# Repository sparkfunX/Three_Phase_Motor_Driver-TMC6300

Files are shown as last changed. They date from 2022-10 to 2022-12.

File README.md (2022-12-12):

SparkFun 3-Phase BLDC Motor Driver - TMC6300
========================================

SparkFun 3-Phase BLDC Motor Driver - TMC6300 (https://www.sparkfun.com/products/21220)

[*SparkFun 3-Phase BLDC Motor Driver - TMC6300(ROB-21220)*](https://www.sparkfun.com/products/21220)

The TMC6300 from Trinamic is a powerful, yet easy to use three phase brushless DC (BLDC) motor driver. Separate high side and low side controls allow for incredible control up to 2A of current. The driver is temperature and short circuit protected with a diagnostic output pin to indicate system issues. With an operating voltage down to 2V, the TMC6300 is suitable for battery powered designs.

We've designed an innovative 2 sided, 4 layer breakout board to make hookup as easy as possible. The board is mounted with LEDs and labels facing up, IC down. This allows the thermal pad on the board to be access if cooling is required. 

Controlling 3-phase BLDC motors is not trivial. This board requires 6 PWM signals to fully control one motor. We've found the [*Arduino Simple Field Oriented Control*](https://docs.simplefoc.com/) library to be very good. The [open loop example](https://github.com/simplefoc/Arduino-FOC/blob/master/examples/motion_control/open_loop_motor_control/open_loop_velocity_example/open_loop_velocity_example.ino) combined with the [6 channel PWM method](https://docs.simplefoc.com/bldcdriver6pwm) and *every* PWM pin on the Arduino Uno gets this board working. Note the [pairs of PWM pins](https://docs.simplefoc.com/bldcdriver6pwm) that must be used. 

This board was designed to control our [3-phase Brushless Gimbal Stabilizer Motor](https://www.sparkfun.com/products/20441) but can be used with any 3-phase motor up to 2A.

SparkFun labored with love to create this code. Feel like supporting open source hardware? 
Buy a [breakout board](https://www.sparkfun.com/products/21220) from SparkFun!

Repository Contents
-------------------

* **/Documents** - Datasheet and User Manual
* **/Hardware** - Eagle design files (.brd, .sch)

License Information
-------------------

This product is _**open source**_! 

Please review the LICENSE.md file for license information. 

If you have any questions or concerns on licensing, please contact techsupport@sparkfun.com.

Please use, reuse, and modify these files as you see fit. Please maintain attribution to SparkFun Electronics and release any derivative under the same license.

Distributed as-is; no warranty is given.

- Your friends at SparkFun.

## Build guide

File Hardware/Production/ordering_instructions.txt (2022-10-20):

panel size, 108x118mm
PCB thickness, 1.6mm
number of layers, 4
soldermask color, Black
silkscreen color, White
oz copper, 1oz
finish, HASL lead free
stencils, none
pcs per panel, 30
min trace width, 0.1778mm / 0.0070in
min drill size, 0.3048mm / 0.0120in
filename to layer stackup 1/2/3/4: GTL, GL2, GL3, GBL

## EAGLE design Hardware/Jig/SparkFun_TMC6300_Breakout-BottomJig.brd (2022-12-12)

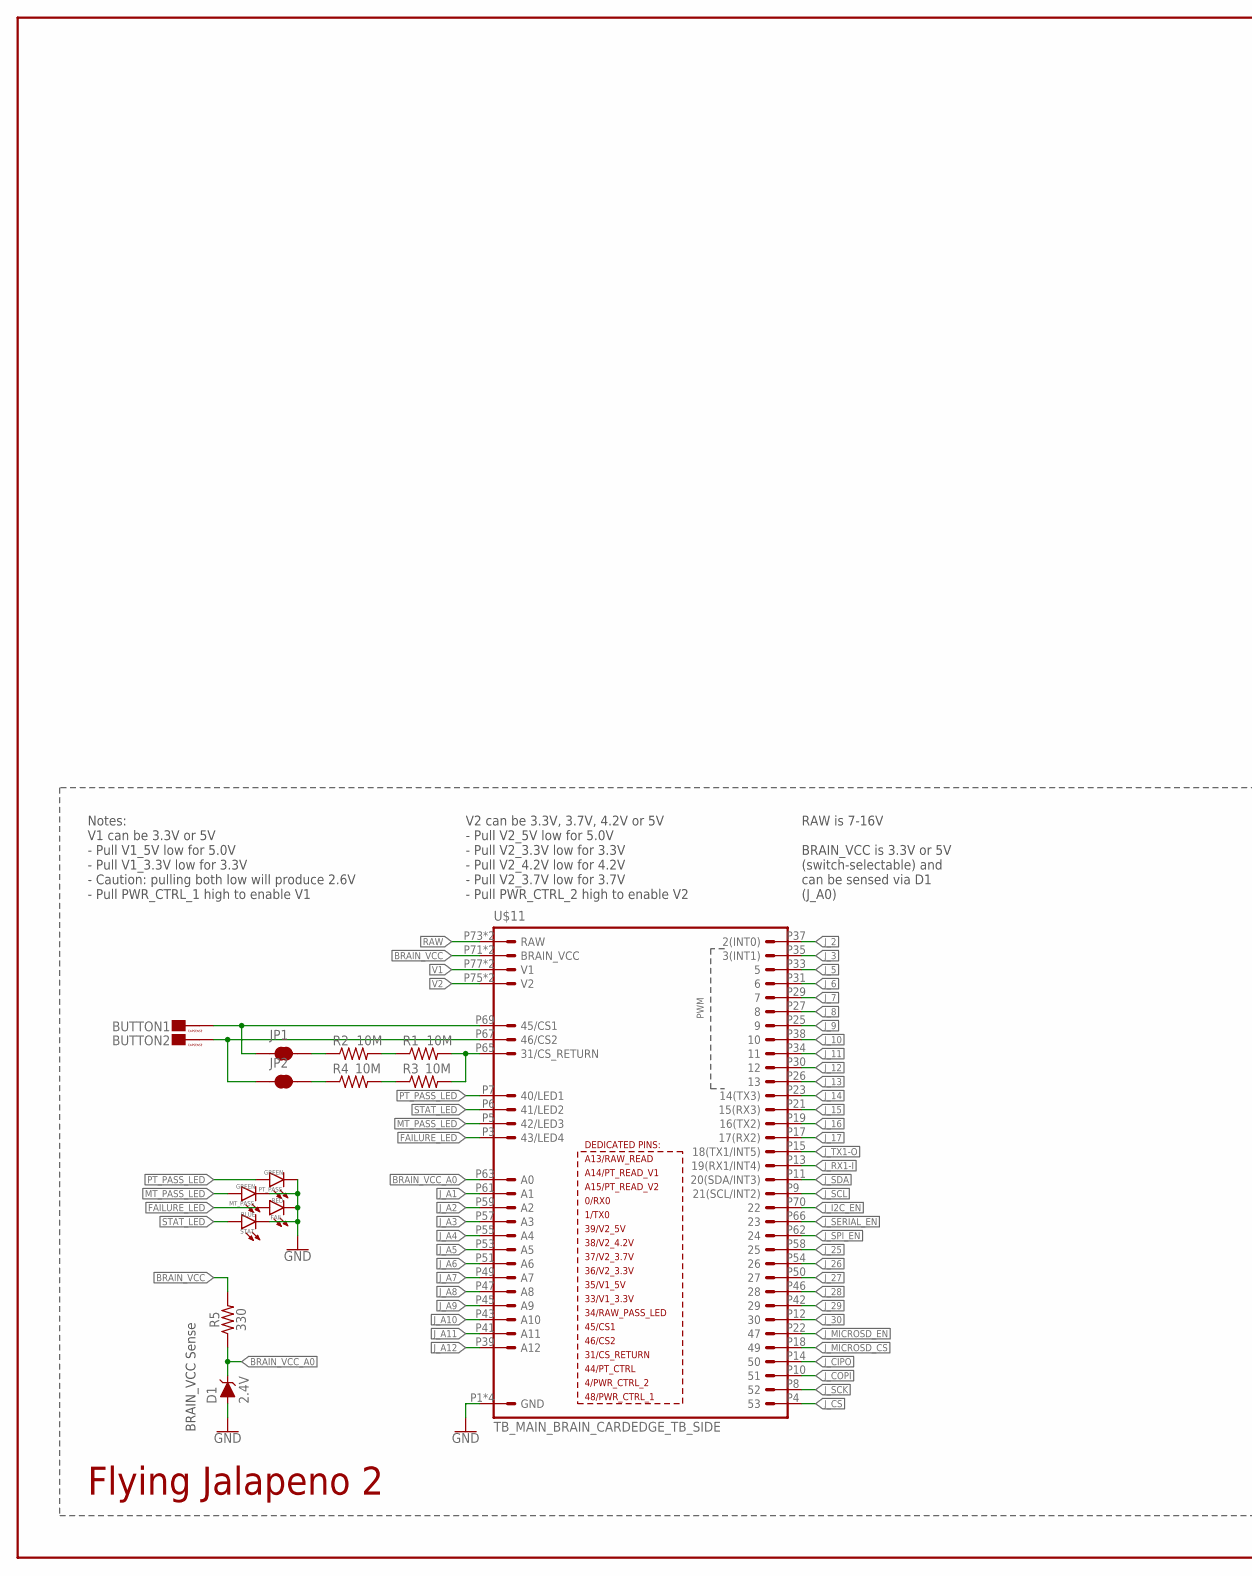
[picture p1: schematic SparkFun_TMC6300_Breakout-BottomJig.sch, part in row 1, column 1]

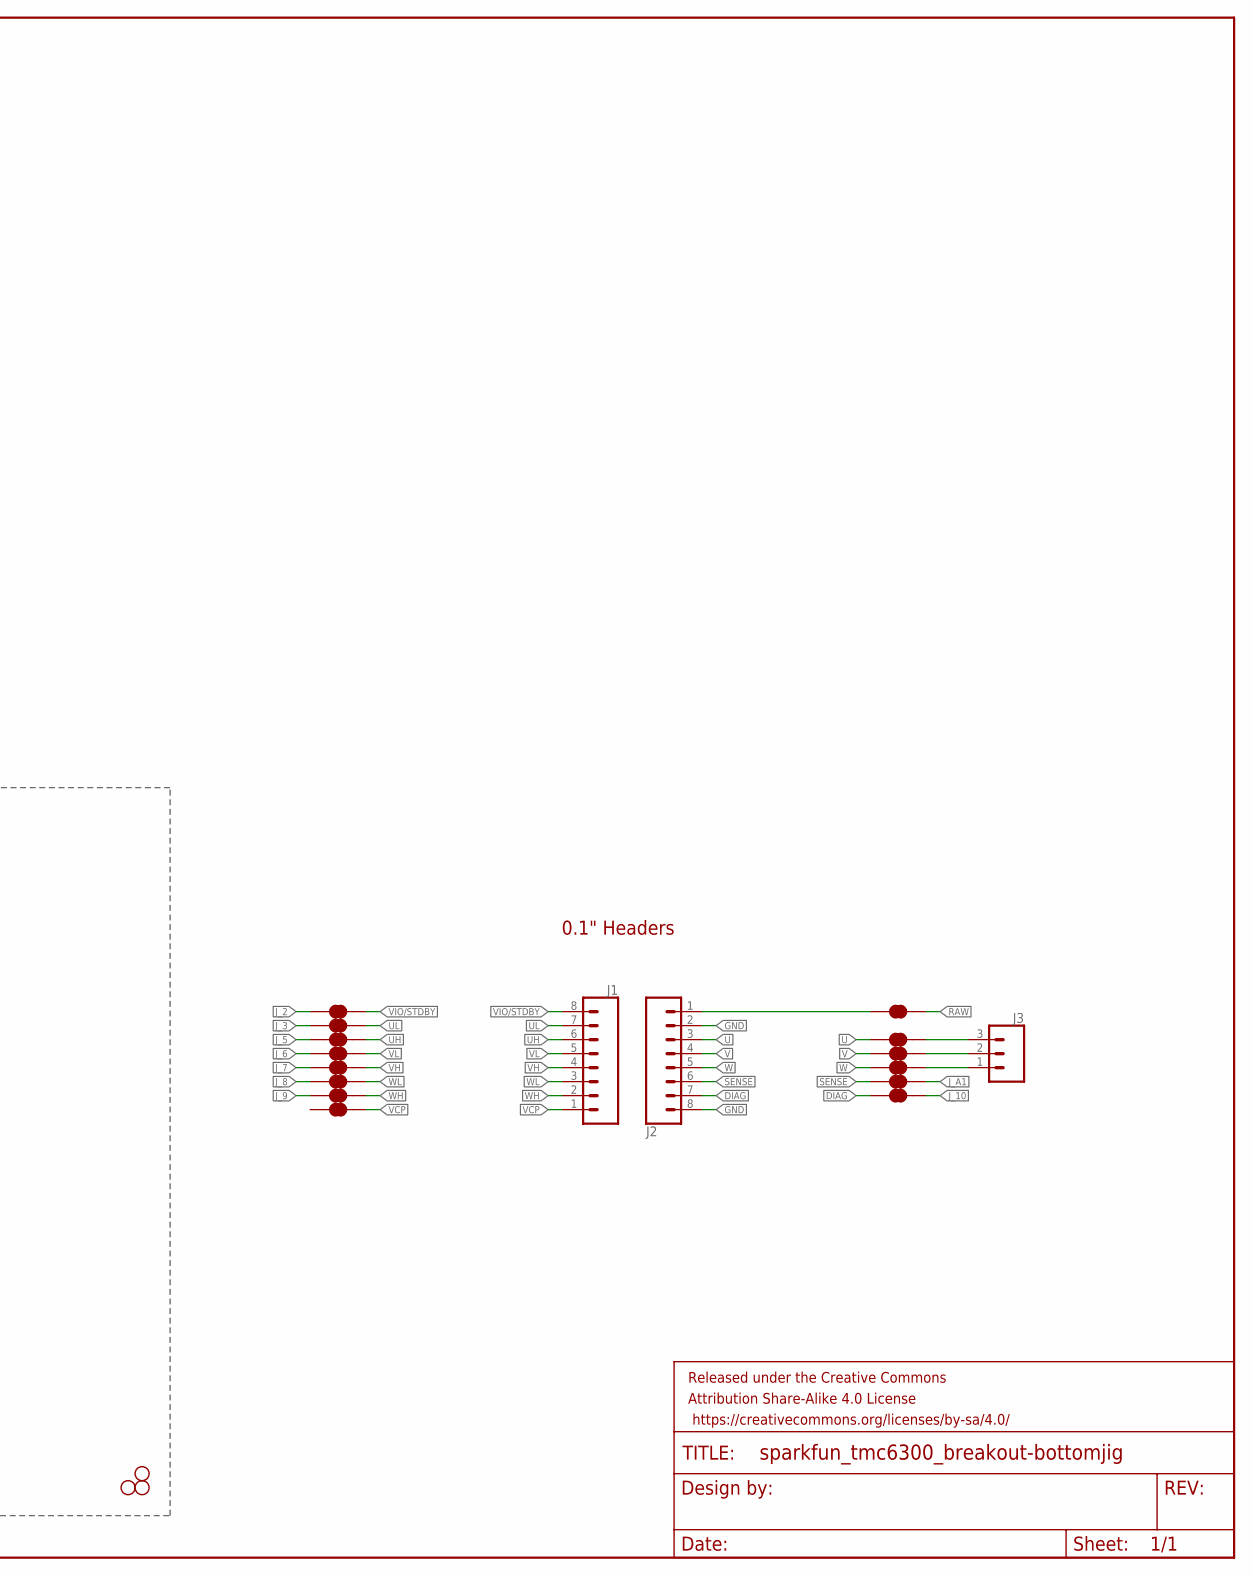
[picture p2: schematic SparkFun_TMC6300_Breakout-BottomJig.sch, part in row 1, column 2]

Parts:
BUTTON1, BUTTON2: CAPSENSE_BUTTON_PAD_ONLYV2_SMALL; CAPSENSE_BUTTON_PAD_ONLY_SM
D1: 2.4V; SOD-323
FAIL: RED; LED-1206
FRAME2: FRAME-LEDGER; CREATIVE_COMMONS
H1, H3, H4: STAND-OFF
J1, J2: CONN_08LOCK_NO_SILK; 1X08_LOCK_NO_SILK
J3: CONN_031X03_NO_SILK; 1X03_NO_SILK
JP1, JP2: JUMPER-SMT_2_NC_TRACE_SILK; SMT-JUMPER_2_NC_TRACE_SILK
J_SCL6, J_SCL7, J_SCL8: JUMPER-SMT_2_NC_TRACE_NO-SILK; SMT-JUMPER_2_NC_TRACE_NO-SILK
J_SDA1, J_SDA2, J_SDA3, J_SDA4, J_SDA5, J_SDA6, J_SDA7, J_SDA8, J_SDA9, J_SDA10, J_SDA11: JUMPER-SMT_2_NC_TRACE_NO-SILK; SMT-JUMPER_2_NC_TRACE_NO-SILK
MT_PASS: GREEN; LED-1206
PT_PASS: GREEN; LED-1206
R1, R2, R3, R4: 10M; 0603
R5: 330; 0603
STAT: BLUE; LED-1206
U$11: TB_MAIN_BRAIN_CARDEDGE_TB_SIDE; TB_CARDEDGE

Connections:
BRAIN_VCC: R5.2, U$11.P71 (BRAIN_VCC), U$11.P72 (BRAIN_VCC)
BRAIN_VCC_A0: D1.C, R5.1, U$11.P63 (A0)
DIAG: J2.7, J_SDA7.1
FAILURE_LED: FAIL.A, U$11.P3 (43/LED4)
GND: D1.A, FAIL.C, J2.2, J2.8, MT_PASS.C, PT_PASS.C, STAT.C, U$11.P1 (GND), U$11.P2 (GND), U$11.P79 (GND), U$11.P80 (GND)
J_2: J_SCL8.1, U$11.P37 (2(INT0))
J_3: J_SCL6.1, U$11.P35 (3(INT1))
J_5: J_SCL7.1, U$11.P33 (5)
J_6: J_SDA2.1, U$11.P31 (6)
J_7: J_SDA3.1, U$11.P29 (7)
J_8: J_SDA4.1, U$11.P27 (8)
J_9: J_SDA5.1, U$11.P25 (9)
J_10: J_SDA7.2, U$11.P38 (10)
J_11: U$11.P34 (11)
J_12: U$11.P30 (12)
J_13: U$11.P26 (13)
J_14: U$11.P23 (14(TX3))
J_15: U$11.P21 (15(RX3))
J_16: U$11.P19 (16(TX2))
J_17: U$11.P17 (17(RX2))
J_25: U$11.P58 (25)
J_26: U$11.P54 (26)
J_27: U$11.P50 (27)
J_28: U$11.P46 (28)
J_29: U$11.P42 (29)
J_30: U$11.P12 (30)
J_A1: J_SDA8.2, U$11.P61 (A1)
J_A2: U$11.P59 (A2)
J_A3: U$11.P57 (A3)
J_A4: U$11.P55 (A4)
J_A5: U$11.P53 (A5)
J_A6: U$11.P51 (A6)
J_A7: U$11.P49 (A7)
J_A8: U$11.P47 (A8)
J_A9: U$11.P45 (A9)
J_A10: U$11.P43 (A10)
J_A11: U$11.P41 (A11)
J_A12: U$11.P39 (A12)
J_CIPO: U$11.P14 (50)
J_COPI: U$11.P10 (51)
J_CS: U$11.P4 (53)
J_I2C_EN: U$11.P70 (22)
J_MICROSD_!CS!: U$11.P18 (49)
J_MICROSD_EN: U$11.P22 (47)
J_RX1-I: U$11.P13 (19(RX1/INT4))
J_SCK: U$11.P8 (52)
J_SCL: U$11.P9 (21(SCL/INT2))
J_SDA: U$11.P11 (20(SDA/INT3))
J_SERIAL_EN: U$11.P66 (23)
J_SPI_EN: U$11.P62 (24)
J_TX1-O: U$11.P15 (18(TX1/INT5))
MT_PASS_LED: MT_PASS.A, U$11.P5 (42/LED3)
unnamed: J3.1, J_SDA9.2
unnamed: R1.2, R3.2, U$11.P65 (31/CS_RETURN)
unnamed: R1.1, R2.2
unnamed: J3.2, J_SDA10.2
unnamed: J3.3, J_SDA11.2
unnamed: J2.1, J_SDA1.1
unnamed: BUTTON1.CAPSENSE_PAD, JP1.1, U$11.P69 (45/CS1)
unnamed: R3.1, R4.2
unnamed: JP2.2, R4.1
unnamed: BUTTON2.CAPSENSE_PAD, JP2.1, U$11.P67 (46/CS2)
unnamed: JP1.2, R2.1
PT_PASS_LED: PT_PASS.A, U$11.P7 (40/LED1)
RAW: J_SDA1.2, U$11.P73 (RAW), U$11.P74 (RAW)
SENSE: J2.6, J_SDA8.1
STAT_LED: STAT.A, U$11.P6 (41/LED2)
U: J2.3, J_SDA11.1
UH: J1.6, J_SCL7.2
UL: J1.7, J_SCL6.2
V: J2.4, J_SDA10.1
V1: U$11.P77 (V1), U$11.P78 (V1)
V2: U$11.P75 (V2), U$11.P76 (V2)
VCP: J1.1, J_SDA6.2
VH: J1.4, J_SDA3.2
VIO/!STDBY!: J1.8, J_SCL8.2
VL: J1.5, J_SDA2.2
W: J2.5, J_SDA9.1
WH: J1.2, J_SDA5.2
WL: J1.3, J_SDA4.2

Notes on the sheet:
0.1" Headers
Flying Jalapeno 2
Notes: V1 can be 3.3V or 5V - Pull V1_5V low for 5.0V - Pull V1_3.3V low for 3.3V - Caution: pulling both low will produce 2.6V - Pull PWR_CTRL_1 high to enable V1
V2 can be 3.3V, 3.7V, 4.2V or 5V - Pull V2_5V low for 5.0V - Pull V2_3.3V low for 3.3V - Pull V2_4.2V low for 4.2V - Pull V2_3.7V low for 3.7V - Pull PWR_CTRL_2 high to enable V2
RAW is 7-16V BRAIN_VCC is 3.3V or 5V (switch-selectable) and can be sensed via D1 (J_A0)
BRAIN_VCC Sense

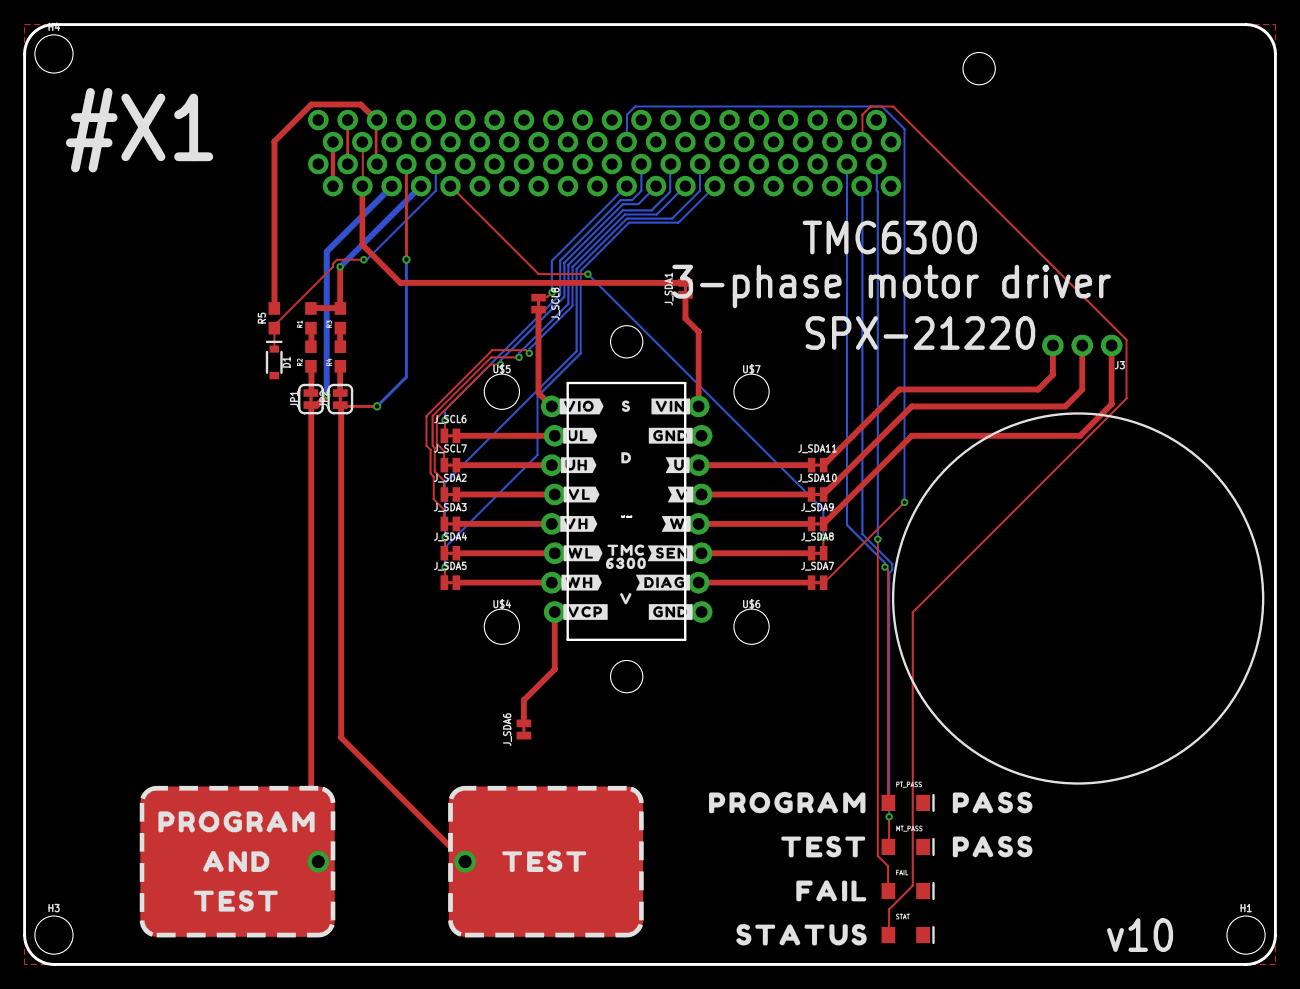
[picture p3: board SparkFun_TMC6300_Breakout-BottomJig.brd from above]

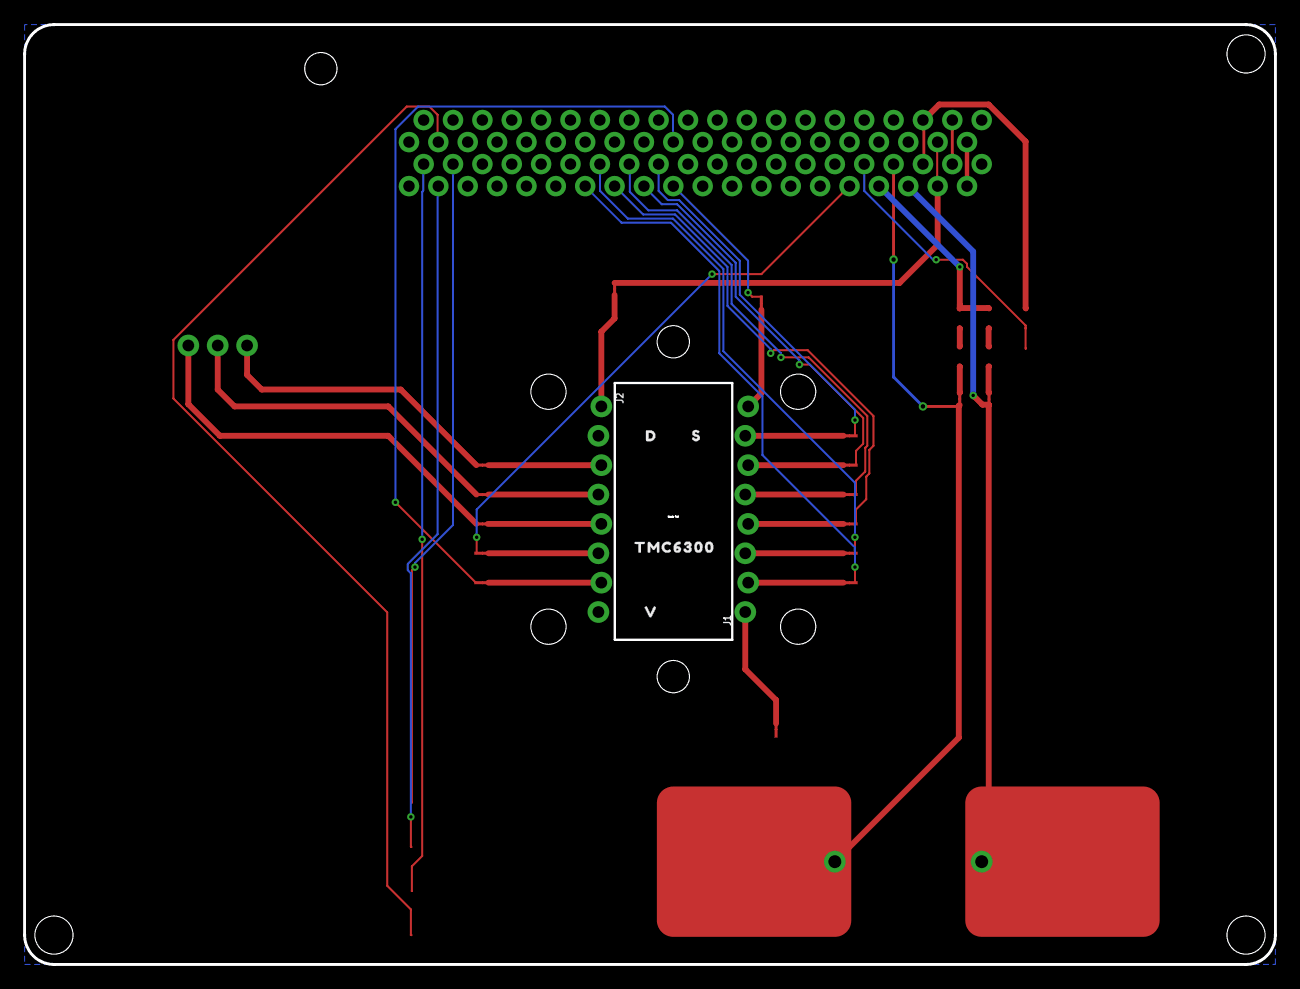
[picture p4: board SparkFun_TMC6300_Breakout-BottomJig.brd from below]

Board: 2 copper layers, 108.2 x 81.3 mm, 77 parts (6 on the bottom side), 43 nets.

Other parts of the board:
U$1, U$28: #GND#1
U$2: #SEN#0
U$3: #DIAG#0
U$4, U$5, U$6, U$7: STAND-OFF-TIGHT
U$8, U$10: NUBBIN_LOCKER
U$9: #U#6
U$12: #VCP#0
U$13: #VIO#1
U$14, U$29: PROGRAM0
U$15: 63001
U$16, U$18: D0
U$17: TMC63000
U$19, U$27: S1
U$20, U$26: V2
U$21: #UH#5
U$22: #UL#4
U$23: TMC0
U$24: #VIN#0
U$25: #V#7
U$30: #VH#2
U$31: #VL#3
U$32: #W#8
U$33: #WH#1
U$34: #WL#0
U$35: AND0
U$38, U$39, U$40: TEST0
U$41, U$42: PASS0
U$43: FAIL0
U$44: STATUS0

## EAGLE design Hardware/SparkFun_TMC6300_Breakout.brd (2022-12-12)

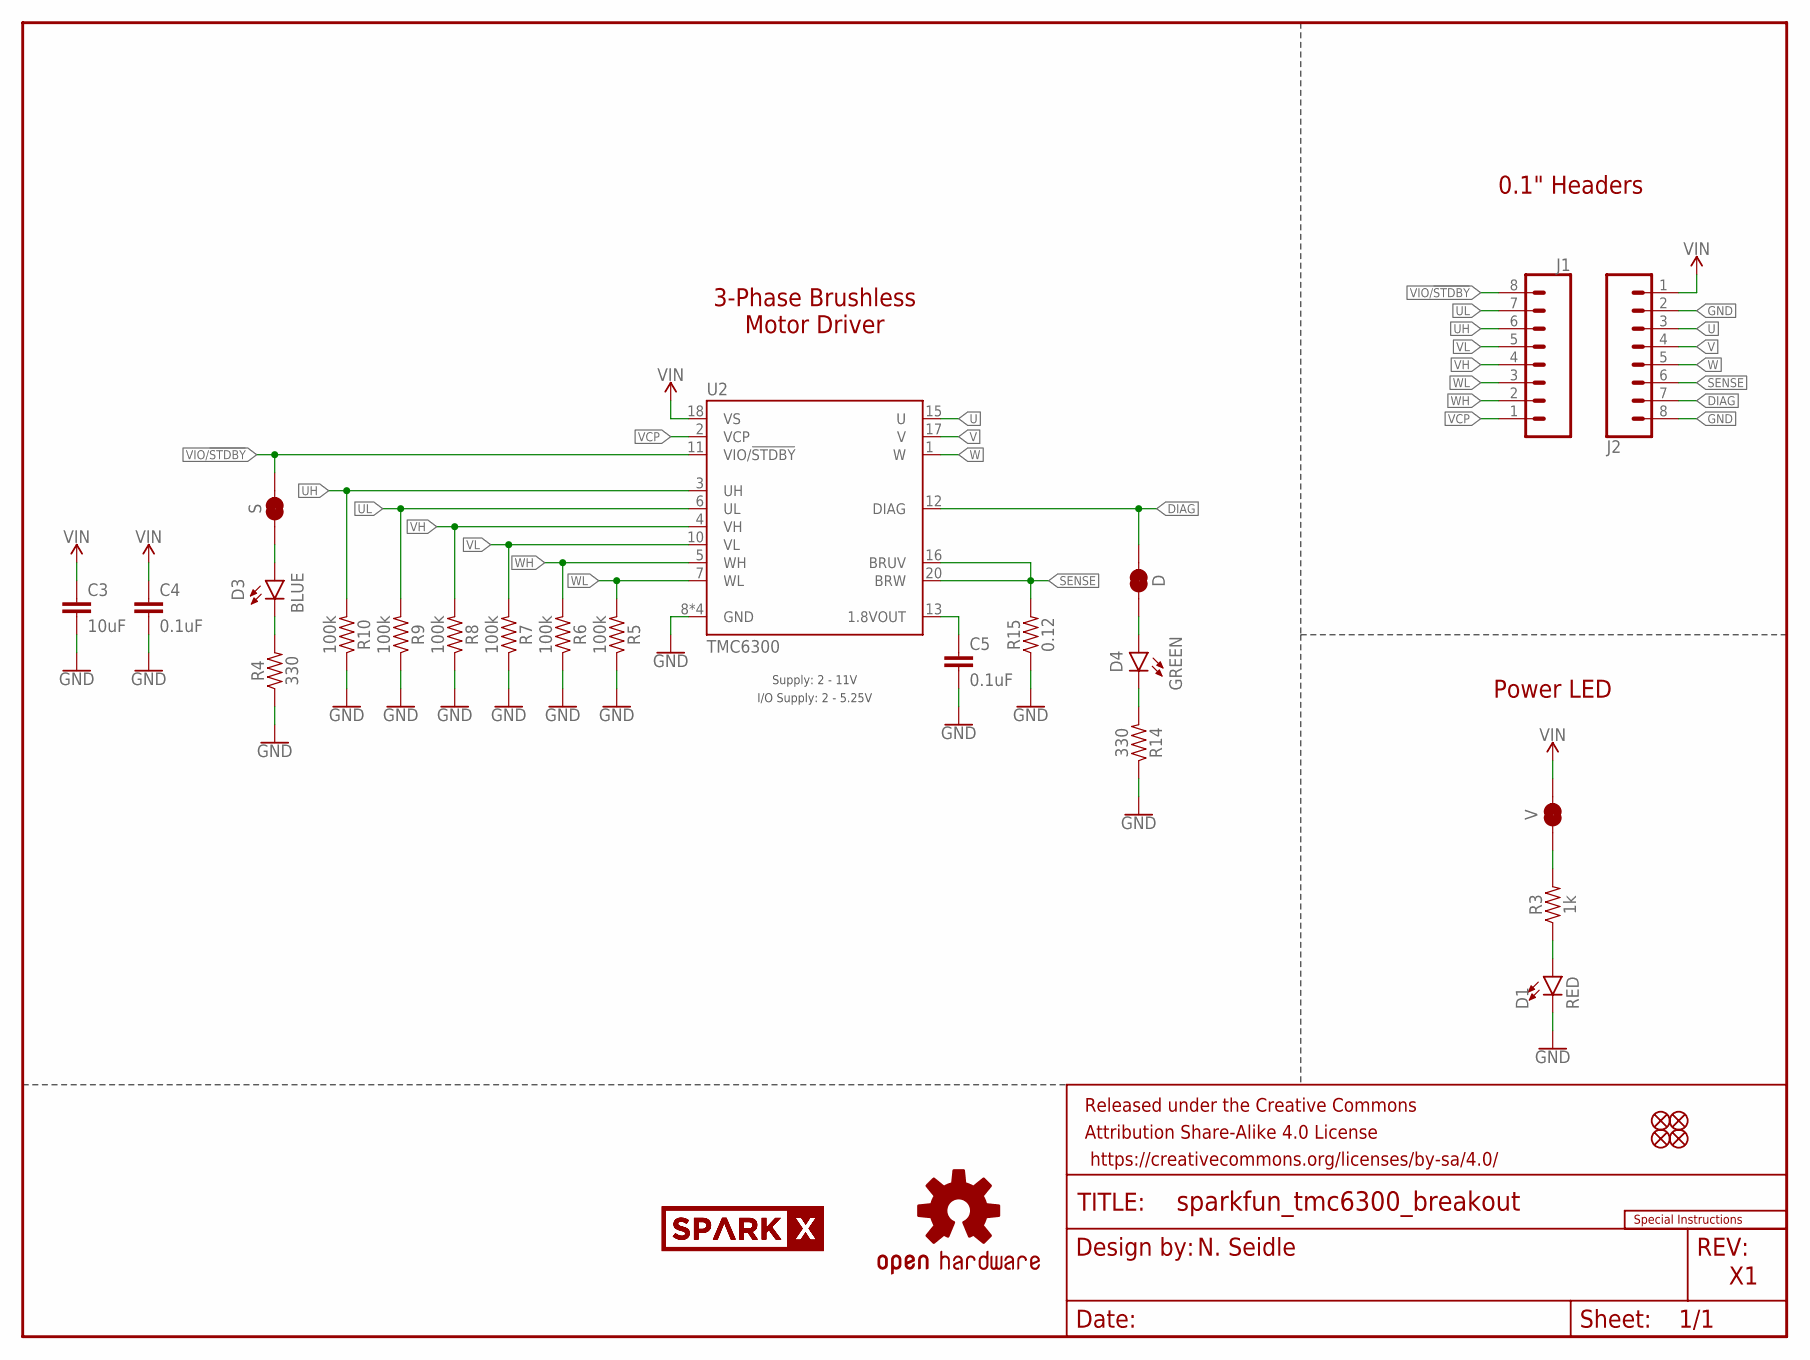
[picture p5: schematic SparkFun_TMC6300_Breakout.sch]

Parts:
C3: 10uF; 0805
C4, C5: 0.1uF; 0603
D: JUMPER-SMT_2_NC_TRACE_SILK; SMT-JUMPER_2_NC_TRACE_SILK
D1: RED; LED-0603
D3: BLUE; LED-0603
D4: GREEN; LED-0603
FD1, FD2, FD3, FD4: FIDUCIALUFIDUCIAL; FIDUCIAL-MICRO
FRAME1: FRAME-LETTER; CREATIVE_COMMONS
J1, J2: CONN_08LOCK_NO_SILK; 1X08_LOCK_NO_SILK
LOGO1: OSHW-LOGONO_SILK; DUMMY
LOGO2: SPECIAL_INSTRUCTIONS-ORDERING; ORDERING_INSTRUCTIONS
R3: 1k; 0603
R4, R14: 330; 0603
R5, R6, R7, R8, R9, R10: 100k; 0603
R15: 0.12; 1206
S: JUMPER-SMT_2_NC_TRACE_SILK; SMT-JUMPER_2_NC_TRACE_SILK
U2: TMC6300; QFN-20
U$36, U$37: SPARKX-LOGO2; SPARKX-TINY
V: JUMPER-SMT_2_NC_TRACE_SILK; SMT-JUMPER_2_NC_TRACE_SILK

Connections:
DIAG: D.2, J2.7, U2.12 (DIAG)
GND: C3.2, C4.2, C5.2, D1.C, J2.2, J2.8, R4.1, R5.1, R6.1, R7.1, R8.1, R9.1, R10.1, R14.1, R15.1, U2.8 (GND), U2.9 (GND), U2.14 (GND), U2.PAD (GND)
unnamed: R3.2, V.1
unnamed: D1.A, R3.1
unnamed: D3.A, S.1
unnamed: C5.1, U2.13 (1.8VOUT)
unnamed: D.1, D4.A
unnamed: D3.C, R4.2
unnamed: D4.C, R14.2
SENSE: J2.6, R15.2, U2.16 (BRUV), U2.20 (BRW)
U: J2.3, U2.15 (U)
UH: J1.6, R10.2, U2.3 (UH)
UL: J1.7, R9.2, U2.6 (UL)
V: J2.4, U2.17 (V)
VCP: J1.1, U2.2 (VCP)
VH: J1.4, R8.2, U2.4 (VH)
VIN: C3.1, C4.1, J2.1, U2.18 (VS), V.2
VIO/!STDBY!: J1.8, S.2, U2.11 (VIO/!STDBY!)
VL: J1.5, R7.2, U2.10 (VL)
W: J2.5, U2.1 (W)
WH: J1.2, R6.2, U2.5 (WH)
WL: J1.3, R5.2, U2.7 (WL)

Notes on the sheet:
0.1" Headers
Power LED
Supply: 2 - 11V
I/O Supply: 2 - 5.25V
3-Phase Brushless Motor Driver
N. Seidle

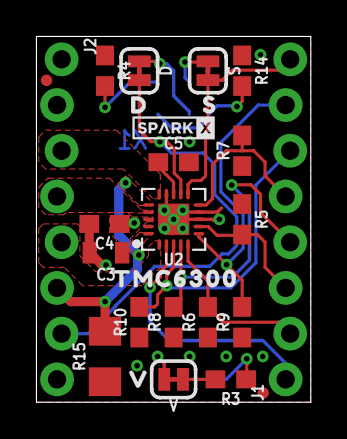
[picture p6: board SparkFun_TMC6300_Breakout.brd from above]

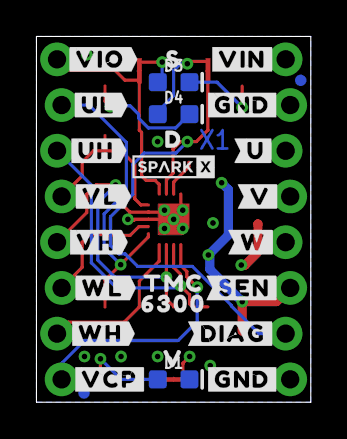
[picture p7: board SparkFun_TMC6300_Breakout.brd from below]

Board: 4 copper layers, 15.2 x 20.3 mm, 56 parts (28 on the bottom side), 22 nets.

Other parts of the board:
U$1, U$28: #GND#1
U$2: #SEN#0
U$3: #DIAG#0
U$9: #U#6
U$12: #VCP#0
U$13: #VIO#1
U$15: 63001
U$16, U$18: D0
U$17: TMC63000
U$19, U$27: S1
U$20, U$26: V2
U$21: #UH#5
U$22: #UL#4
U$23: TMC0
U$24: #VIN#0
U$25: #V#7
U$30: #VH#2
U$31: #VL#3
U$32: #W#8
U$33: #WH#1
U$34: #WL#0

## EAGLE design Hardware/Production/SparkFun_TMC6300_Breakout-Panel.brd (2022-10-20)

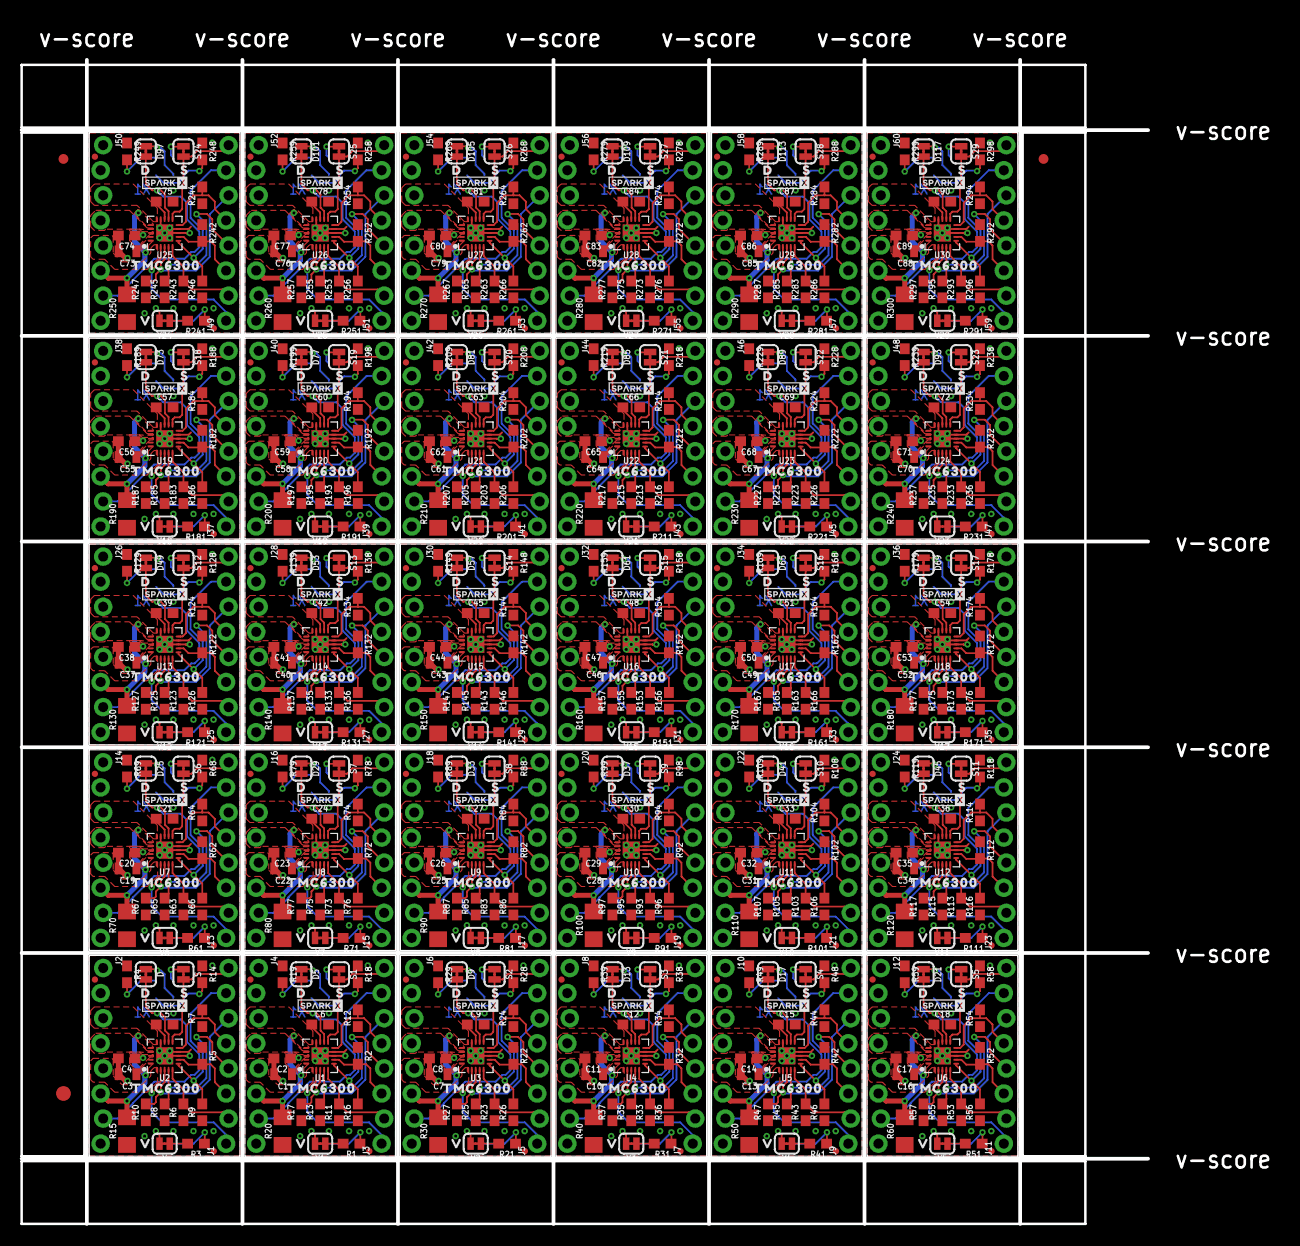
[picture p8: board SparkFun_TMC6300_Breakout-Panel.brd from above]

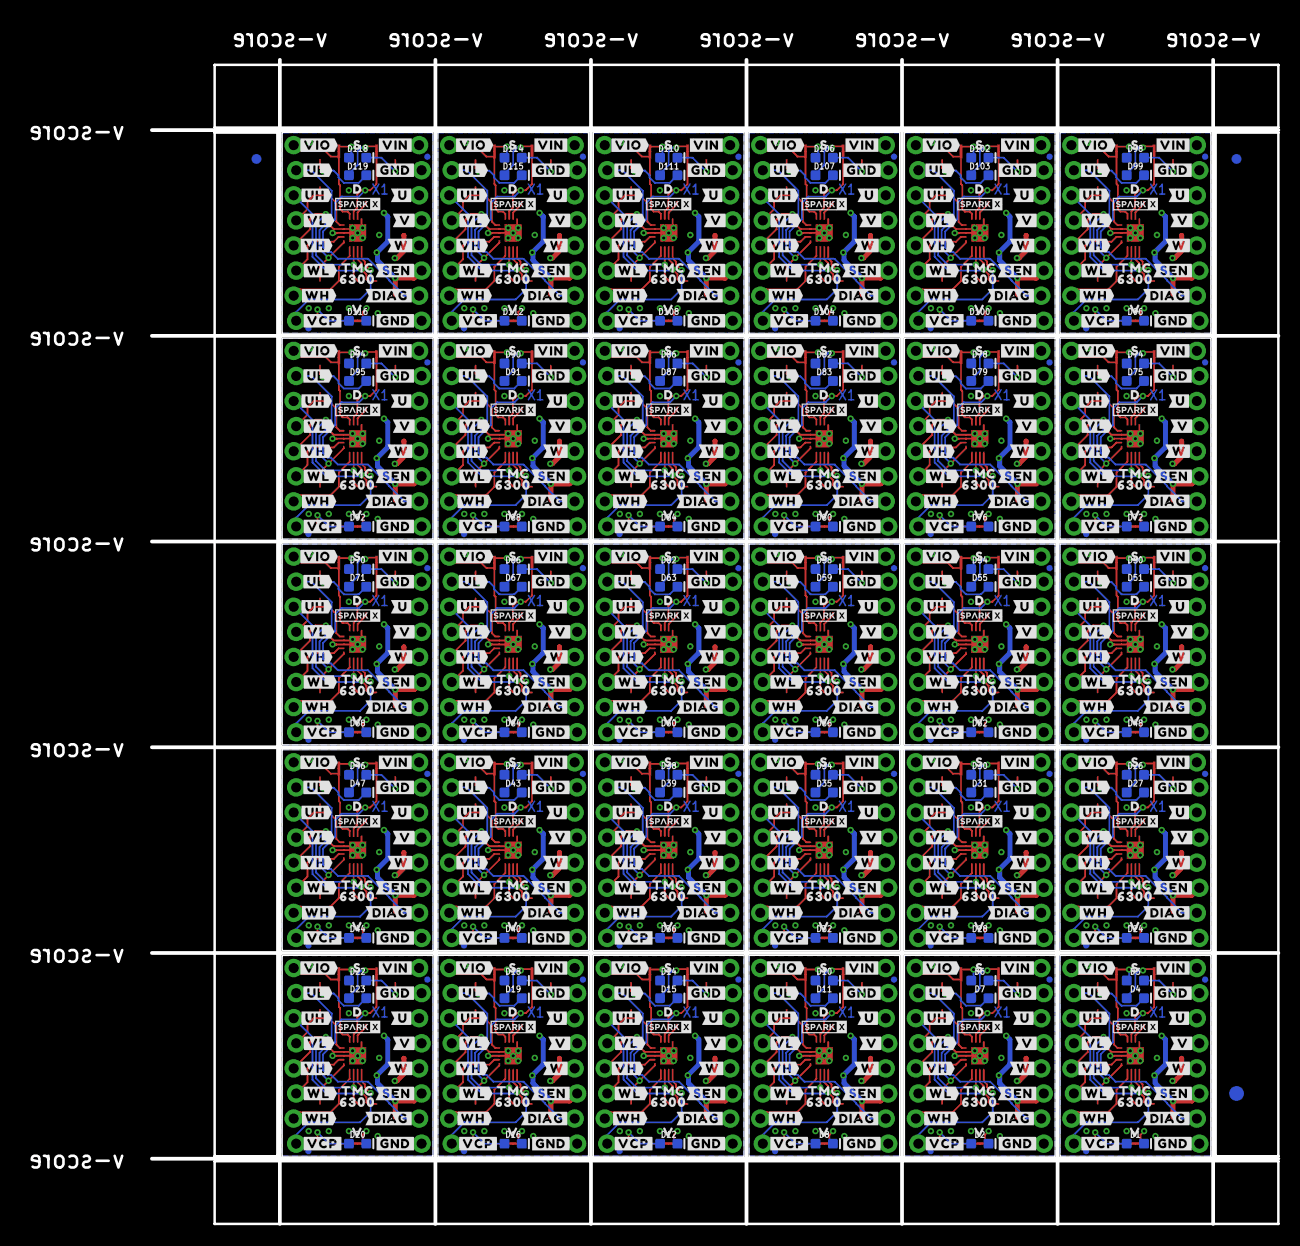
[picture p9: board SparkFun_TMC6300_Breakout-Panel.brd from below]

Board: 4 copper layers, 114.0 x 117.9 mm, 1596 parts (813 on the bottom side), 660 nets.

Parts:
C1, C3, C7, C10, C13, C16, C19, C22, C25, C28, C31, C34, C37, C40, C43, C46, C49, C52, C55, C58, C61, C64, C67, C70, C73, C76, C79, C82, C85, C88: 10uF; 0805
C2, C4, C5, C6, C8, C9, C11, C12, C14, C15, C17, C18, C20, C21, C23, C24, C26, C27, C29, C30, C32, C33, C35, C36, C38, C39, C41, C42, C44, C45, C47, C48, C50, C51, C53, C54, C56, C57, C59, C60, C62, C63, C65, C66, C68, C69, C71, C72, C74, C75, C77, C78, C80, C81, C83, C84, C86, C87, C89, C90: 0.1uF; 0603
D, D5, D9, D13, D17, D21, D25, D29, D33, D37, D41, D45, D49, D53, D57, D61, D65, D69, D73, D77, D81, D85, D89, D93, D97, D101, D105, D109, D113, D117: JUMPER-SMT_2_NC_TRACE_SILK; SMT-JUMPER_2_NC_TRACE_SILK
D1, D2, D8, D12, D16, D20, D24, D28, D32, D36, D40, D44, D48, D52, D56, D60, D64, D68, D72, D76, D80, D84, D88, D92, D96, D100, D104, D108, D112, D116: RED; LED-0603
D3, D6, D10, D14, D18, D22, D26, D30, D34, D38, D42, D46, D50, D54, D58, D62, D66, D70, D74, D78, D82, D86, D90, D94, D98, D102, D106, D110, D114, D118: BLUE; LED-0603
D4, D7, D11, D15, D19, D23, D27, D31, D35, D39, D43, D47, D51, D55, D59, D63, D67, D71, D75, D79, D83, D87, D91, D95, D99, D103, D107, D111, D115, D119: GREEN; LED-0603
E$1, E$2, E$3, E$4: FIDUCIAL-1X2
E$5, E$6: FIDUCIAL-1.5X3
FD1, FD2, FD3, FD4, FD5, FD6, FD7, FD8, FD9, FD10, FD11, FD12, FD13, FD14, FD15, FD16, FD17, FD18, FD19, FD20, FD21, FD22, FD23, FD24, FD25, FD26, FD27, FD28, FD29, FD30, FD31, FD32, FD33, FD34, FD35, FD36, FD37, FD38, FD39, FD40, FD41, FD42, FD43, FD44, FD45, FD46, FD47, FD48, FD49, FD50, FD51, FD52, FD53, FD54, FD55, FD56, FD57, FD58, FD59, FD60, FD61, FD62, FD63, FD64, FD65, FD66, FD67, FD68, FD69, FD70, FD71, FD72, FD73, FD74, FD75, FD76, FD77, FD78, FD79, FD80, FD81, FD82, FD83, FD84, FD85, FD86, FD87, FD88, FD89, FD90, FD91, FD92, FD93, FD94, FD95, FD96, FD97, FD98, FD99, FD100, FD101, FD102, FD103, FD104, FD105, FD106, FD107, FD108, FD109, FD110, FD111, FD112, FD113, FD114, FD115, FD116, FD117, FD118, FD119, FD120: FIDUCIALUFIDUCIAL; FIDUCIAL-MICRO
J1, J2, J3, J4, J5, J6, J7, J8, J9, J10, J11, J12, J13, J14, J15, J16, J17, J18, J19, J20, J21, J22, J23, J24, J25, J26, J27, J28, J29, J30, J31, J32, J33, J34, J35, J36, J37, J38, J39, J40, J41, J42, J43, J44, J45, J46, J47, J48, J49, J50, J51, J52, J53, J54, J55, J56, J57, J58, J59, J60: 1X08_LOCK_NO_SILK
R1, R3, R21, R31, R41, R51, R61, R71, R81, R91, R101, R111, R121, R131, R141, R151, R161, R171, R181, R191, R201, R211, R221, R231, R241, R251, R261, R271, R281, R291: 1k; 0603
R2, R5, R6, R7, R8, R9, R10, R11, R12, R13, R16, R17, R22, R23, R24, R25, R26, R27, R32, R33, R34, R35, R36, R37, R42, R43, R44, R45, R46, R47, R52, R53, R54, R55, R56, R57, R62, R63, R64, R65, R66, R67, R72, R73, R74, R75, R76, R77, R82, R83, R84, R85, R86, R87, R92, R93, R94, R95, R96, R97, R102, R103, R104, R105, R106, R107, R112, R113, R114, R115, R116, R117, R122, R123, R124, R125, R126, R127, R132, R133, R134, R135, R136, R137, R142, R143, R144, R145, R146, R147, R152, R153, R154, R155, R156, R157, R162, R163, R164, R165, R166, R167, R172, R173, R174, R175, R176, R177, R182, R183, R184, R185, R186, R187, R192, R193, R194, R195, R196, R197, R202, R203, R204, R205, R206, R207, R212, R213, R214, R215, R216, R217, R222, R223, R224, R225, R226, R227, R232, R233, R234, R235, R236, R237, R242, R243, R244, R245, R246, R247, R252, R253, R254, R255, R256, R257, R262, R263, R264, R265, R266, R267, R272, R273, R274, R275, R276, R277, R282, R283, R284, R285, R286, R287, R292, R293, R294, R295, R296, R297: 100k; 0603
R4, R14, R18, R19, R28, R29, R38, R39, R48, R49, R58, R59, R68, R69, R78, R79, R88, R89, R98, R99, R108, R109, R118, R119, R128, R129, R138, R139, R148, R149, R158, R159, R168, R169, R178, R179, R188, R189, R198, R199, R208, R209, R218, R219, R228, R229, R238, R239, R248, R249, R258, R259, R268, R269, R278, R279, R288, R289, R298, R299: 330; 0603
R15, R20, R30, R40, R50, R60, R70, R80, R90, R100, R110, R120, R130, R140, R150, R160, R170, R180, R190, R200, R210, R220, R230, R240, R250, R260, R270, R280, R290, R300: 0.12; 1206
S, S1, S2, S3, S4, S5, S6, S7, S8, S9, S10, S11, S12, S13, S14, S15, S16, S17, S18, S19, S20, S21, S22, S23, S24, S25, S26, S27, S28, S29: JUMPER-SMT_2_NC_TRACE_SILK; SMT-JUMPER_2_NC_TRACE_SILK
U1, U2, U3, U4, U5, U6, U7, U8, U9, U10, U11, U12, U13, U14, U15, U16, U17, U18, U19, U20, U21, U22, U23, U24, U25, U26, U27, U28, U29, U30: TMC6300; QFN-20
U$1, U$6, U$28, U$43, U$57, U$70, U$84, U$97, U$111, U$124, U$138, U$151, U$165, U$178, U$192, U$205, U$219, U$232, U$246, U$259, U$273, U$286, U$300, U$313, U$327, U$340, U$354, U$367, U$381, U$394, U$408, U$421, U$435, U$448, U$462, U$475, U$489, U$502, U$516, U$529, U$543, U$556, U$570, U$583, U$597, U$610, U$624, U$637, U$651, U$664, U$678, U$691, U$705, U$718, U$732, U$745, U$759, U$772, U$786, U$799: #GND#1
U$2, U$53, U$80, U$107, U$134, U$161, U$188, U$215, U$242, U$269, U$296, U$323, U$350, U$377, U$404, U$431, U$458, U$485, U$512, U$539, U$566, U$593, U$620, U$647, U$674, U$701, U$728, U$755, U$782, U$809: #SEN#0
U$3, U$54, U$81, U$108, U$135, U$162, U$189, U$216, U$243, U$270, U$297, U$324, U$351, U$378, U$405, U$432, U$459, U$486, U$513, U$540, U$567, U$594, U$621, U$648, U$675, U$702, U$729, U$756, U$783, U$810: #DIAG#0
U$4, U$5, U$36, U$37, U$55, U$56, U$82, U$83, U$109, U$110, U$136, U$137, U$163, U$164, U$190, U$191, U$217, U$218, U$244, U$245, U$271, U$272, U$298, U$299, U$325, U$326, U$352, U$353, U$379, U$380, U$406, U$407, U$433, U$434, U$460, U$461, U$487, U$488, U$514, U$515, U$541, U$542, U$568, U$569, U$595, U$596, U$622, U$623, U$649, U$650, U$676, U$677, U$703, U$704, U$730, U$731, U$757, U$758, U$784, U$785: SPARKX-LOGO2; SPARKX-TINY
U$7, U$12, U$58, U$85, U$112, U$139, U$166, U$193, U$220, U$247, U$274, U$301, U$328, U$355, U$382, U$409, U$436, U$463, U$490, U$517, U$544, U$571, U$598, U$625, U$652, U$679, U$706, U$733, U$760, U$787: #VCP#0
U$8, U$13, U$59, U$86, U$113, U$140, U$167, U$194, U$221, U$248, U$275, U$302, U$329, U$356, U$383, U$410, U$437, U$464, U$491, U$518, U$545, U$572, U$599, U$626, U$653, U$680, U$707, U$734, U$761, U$788: #VIO#1
U$9, U$44, U$71, U$98, U$125, U$152, U$179, U$206, U$233, U$260, U$287, U$314, U$341, U$368, U$395, U$422, U$449, U$476, U$503, U$530, U$557, U$584, U$611, U$638, U$665, U$692, U$719, U$746, U$773, U$800: #U#6
U$10, U$17, U$60, U$87, U$114, U$141, U$168, U$195, U$222, U$249, U$276, U$303, U$330, U$357, U$384, U$411, U$438, U$465, U$492, U$519, U$546, U$573, U$600, U$627, U$654, U$681, U$708, U$735, U$762, U$789: TMC63000
U$11, U$16, U$18, U$35, U$61, U$64, U$88, U$91, U$115, U$118, U$142, U$145, U$169, U$172, U$196, U$199, U$223, U$226, U$250, U$253, U$277, U$280, U$304, U$307, U$331, U$334, U$358, U$361, U$385, U$388, U$412, U$415, U$439, U$442, U$466, U$469, U$493, U$496, U$520, U$523, U$547, U$550, U$574, U$577, U$601, U$604, U$628, U$631, U$655, U$658, U$682, U$685, U$709, U$712, U$736, U$739, U$763, U$766, U$790, U$793: D0
U$14, U$20, U$26, U$39, U$62, U$66, U$89, U$93, U$116, U$120, U$143, U$147, U$170, U$174, U$197, U$201, U$224, U$228, U$251, U$255, U$278, U$282, U$305, U$309, U$332, U$336, U$359, U$363, U$386, U$390, U$413, U$417, U$440, U$444, U$467, U$471, U$494, U$498, U$521, U$525, U$548, U$552, U$575, U$579, U$602, U$606, U$629, U$633, U$656, U$660, U$683, U$687, U$710, U$714, U$737, U$741, U$764, U$768, U$791, U$795: V2
U$15, U$40, U$67, U$94, U$121, U$148, U$175, U$202, U$229, U$256, U$283, U$310, U$337, U$364, U$391, U$418, U$445, U$472, U$499, U$526, U$553, U$580, U$607, U$634, U$661, U$688, U$715, U$742, U$769, U$796: 63001
U$19, U$27, U$29, U$38, U$63, U$65, U$90, U$92, U$117, U$119, U$144, U$146, U$171, U$173, U$198, U$200, U$225, U$227, U$252, U$254, U$279, U$281, U$306, U$308, U$333, U$335, U$360, U$362, U$387, U$389, U$414, U$416, U$441, U$443, U$468, U$470, U$495, U$497, U$522, U$524, U$549, U$551, U$576, U$578, U$603, U$605, U$630, U$632, U$657, U$659, U$684, U$686, U$711, U$713, U$738, U$740, U$765, U$767, U$792, U$794: S1
U$21, U$45, U$72, U$99, U$126, U$153, U$180, U$207, U$234, U$261, U$288, U$315, U$342, U$369, U$396, U$423, U$450, U$477, U$504, U$531, U$558, U$585, U$612, U$639, U$666, U$693, U$720, U$747, U$774, U$801: #UH#5
U$22, U$46, U$73, U$100, U$127, U$154, U$181, U$208, U$235, U$262, U$289, U$316, U$343, U$370, U$397, U$424, U$451, U$478, U$505, U$532, U$559, U$586, U$613, U$640, U$667, U$694, U$721, U$748, U$775, U$802: #UL#4
U$23, U$41, U$68, U$95, U$122, U$149, U$176, U$203, U$230, U$257, U$284, U$311, U$338, U$365, U$392, U$419, U$446, U$473, U$500, U$527, U$554, U$581, U$608, U$635, U$662, U$689, U$716, U$743, U$770, U$797: TMC0
U$24, U$42, U$69, U$96, U$123, U$150, U$177, U$204, U$231, U$258, U$285, U$312, U$339, U$366, U$393, U$420, U$447, U$474, U$501, U$528, U$555, U$582, U$609, U$636, U$663, U$690, U$717, U$744, U$771, U$798: #VIN#0
U$25, U$47, U$74, U$101, U$128, U$155, U$182, U$209, U$236, U$263, U$290, U$317, U$344, U$371, U$398, U$425, U$452, U$479, U$506, U$533, U$560, U$587, U$614, U$641, U$668, U$695, U$722, U$749, U$776, U$803: #V#7
U$30, U$48, U$75, U$102, U$129, U$156, U$183, U$210, U$237, U$264, U$291, U$318, U$345, U$372, U$399, U$426, U$453, U$480, U$507, U$534, U$561, U$588, U$615, U$642, U$669, U$696, U$723, U$750, U$777, U$804: #VH#2
U$31, U$49, U$76, U$103, U$130, U$157, U$184, U$211, U$238, U$265, U$292, U$319, U$346, U$373, U$400, U$427, U$454, U$481, U$508, U$535, U$562, U$589, U$616, U$643, U$670, U$697, U$724, U$751, U$778, U$805: #VL#3
U$32, U$50, U$77, U$104, U$131, U$158, U$185, U$212, U$239, U$266, U$293, U$320, U$347, U$374, U$401, U$428, U$455, U$482, U$509, U$536, U$563, U$590, U$617, U$644, U$671, U$698, U$725, U$752, U$779, U$806: #W#8
U$33, U$51, U$78, U$105, U$132, U$159, U$186, U$213, U$240, U$267, U$294, U$321, U$348, U$375, U$402, U$429, U$456, U$483, U$510, U$537, U$564, U$591, U$618, U$645, U$672, U$699, U$726, U$753, U$780, U$807: #WH#1
U$34, U$52, U$79, U$106, U$133, U$160, U$187, U$214, U$241, U$268, U$295, U$322, U$349, U$376, U$403, U$430, U$457, U$484, U$511, U$538, U$565, U$592, U$619, U$646, U$673, U$700, U$727, U$754, U$781, U$808: #WL#0
V, V1, V2, V3, V4, V5, V6, V7, V8, V9, V10, V11, V12, V13, V14, V15, V16, V17, V18, V19, V20, V21, V22, V23, V24, V25, V26, V27, V28, V29: JUMPER-SMT_2_NC_TRACE_SILK; SMT-JUMPER_2_NC_TRACE_SILK

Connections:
DIAG: D.2, J2.7, U2.12
DIAG1: D5.2, J4.7, U1.12
DIAG2: D9.2, J6.7, U3.12
DIAG3: D13.2, J8.7, U4.12
DIAG4: D17.2, J10.7, U5.12
DIAG5: D21.2, J12.7, U6.12
DIAG6: D25.2, J14.7, U7.12
DIAG7: D29.2, J16.7, U8.12
DIAG8: D33.2, J18.7, U9.12
DIAG9: D37.2, J20.7, U10.12
DIAG10: D41.2, J22.7, U11.12
DIAG11: D45.2, J24.7, U12.12
DIAG12: D49.2, J26.7, U13.12
DIAG13: D53.2, J28.7, U14.12
DIAG14: D57.2, J30.7, U15.12
DIAG15: D61.2, J32.7, U16.12
DIAG16: D65.2, J34.7, U17.12
DIAG17: D69.2, J36.7, U18.12
DIAG18: D73.2, J38.7, U19.12
DIAG19: D77.2, J40.7, U20.12
DIAG20: D81.2, J42.7, U21.12
DIAG21: D85.2, J44.7, U22.12
DIAG22: D89.2, J46.7, U23.12
DIAG23: D93.2, J48.7, U24.12
DIAG24: D97.2, J50.7, U25.12
DIAG25: D101.2, J52.7, U26.12
DIAG26: D105.2, J54.7, U27.12
DIAG27: D109.2, J56.7, U28.12
DIAG28: D113.2, J58.7, U29.12
DIAG29: D117.2, J60.7, U30.12
GND: C3.2, C4.2, C5.2, D1.C, J2.2, J2.8, R4.1, R5.1, R6.1, R7.1, R8.1, R9.1, R10.1, R14.1, R15.1, U2.8, U2.9, U2.14, U2.PAD
GND1: C1.2, C2.2, C6.2, D2.C, J4.2, J4.8, R2.1, R11.1, R12.1, R13.1, R16.1, R17.1, R18.1, R19.1, R20.1, U1.8, U1.9, U1.14, U1.PAD
GND2: C7.2, C8.2, C9.2, D8.C, J6.2, J6.8, R22.1, R23.1, R24.1, R25.1, R26.1, R27.1, R28.1, R29.1, R30.1, U3.8, U3.9, U3.14, U3.PAD
GND3: C10.2, C11.2, C12.2, D12.C, J8.2, J8.8, R32.1, R33.1, R34.1, R35.1, R36.1, R37.1, R38.1, R39.1, R40.1, U4.8, U4.9, U4.14, U4.PAD
GND4: C13.2, C14.2, C15.2, D16.C, J10.2, J10.8, R42.1, R43.1, R44.1, R45.1, R46.1, R47.1, R48.1, R49.1, R50.1, U5.8, U5.9, U5.14, U5.PAD
GND5: C16.2, C17.2, C18.2, D20.C, J12.2, J12.8, R52.1, R53.1, R54.1, R55.1, R56.1, R57.1, R58.1, R59.1, R60.1, U6.8, U6.9, U6.14, U6.PAD
GND6: C19.2, C20.2, C21.2, D24.C, J14.2, J14.8, R62.1, R63.1, R64.1, R65.1, R66.1, R67.1, R68.1, R69.1, R70.1, U7.8, U7.9, U7.14, U7.PAD
GND7: C22.2, C23.2, C24.2, D28.C, J16.2, J16.8, R72.1, R73.1, R74.1, R75.1, R76.1, R77.1, R78.1, R79.1, R80.1, U8.8, U8.9, U8.14, U8.PAD
GND8: C25.2, C26.2, C27.2, D32.C, J18.2, J18.8, R82.1, R83.1, R84.1, R85.1, R86.1, R87.1, R88.1, R89.1, R90.1, U9.8, U9.9, U9.14, U9.PAD
GND9: C28.2, C29.2, C30.2, D36.C, J20.2, J20.8, R92.1, R93.1, R94.1, R95.1, R96.1, R97.1, R98.1, R99.1, R100.1, U10.8, U10.9, U10.14, U10.PAD
GND10: C31.2, C32.2, C33.2, D40.C, J22.2, J22.8, R102.1, R103.1, R104.1, R105.1, R106.1, R107.1, R108.1, R109.1, R110.1, U11.8, U11.9, U11.14, U11.PAD
GND11: C34.2, C35.2, C36.2, D44.C, J24.2, J24.8, R112.1, R113.1, R114.1, R115.1, R116.1, R117.1, R118.1, R119.1, R120.1, U12.8, U12.9, U12.14, U12.PAD
GND12: C37.2, C38.2, C39.2, D48.C, J26.2, J26.8, R122.1, R123.1, R124.1, R125.1, R126.1, R127.1, R128.1, R129.1, R130.1, U13.8, U13.9, U13.14, U13.PAD
GND13: C40.2, C41.2, C42.2, D52.C, J28.2, J28.8, R132.1, R133.1, R134.1, R135.1, R136.1, R137.1, R138.1, R139.1, R140.1, U14.8, U14.9, U14.14, U14.PAD
GND14: C43.2, C44.2, C45.2, D56.C, J30.2, J30.8, R142.1, R143.1, R144.1, R145.1, R146.1, R147.1, R148.1, R149.1, R150.1, U15.8, U15.9, U15.14, U15.PAD
GND15: C46.2, C47.2, C48.2, D60.C, J32.2, J32.8, R152.1, R153.1, R154.1, R155.1, R156.1, R157.1, R158.1, R159.1, R160.1, U16.8, U16.9, U16.14, U16.PAD
GND16: C49.2, C50.2, C51.2, D64.C, J34.2, J34.8, R162.1, R163.1, R164.1, R165.1, R166.1, R167.1, R168.1, R169.1, R170.1, U17.8, U17.9, U17.14, U17.PAD
GND17: C52.2, C53.2, C54.2, D68.C, J36.2, J36.8, R172.1, R173.1, R174.1, R175.1, R176.1, R177.1, R178.1, R179.1, R180.1, U18.8, U18.9, U18.14, U18.PAD
GND18: C55.2, C56.2, C57.2, D72.C, J38.2, J38.8, R182.1, R183.1, R184.1, R185.1, R186.1, R187.1, R188.1, R189.1, R190.1, U19.8, U19.9, U19.14, U19.PAD
GND19: C58.2, C59.2, C60.2, D76.C, J40.2, J40.8, R192.1, R193.1, R194.1, R195.1, R196.1, R197.1, R198.1, R199.1, R200.1, U20.8, U20.9, U20.14, U20.PAD
GND20: C61.2, C62.2, C63.2, D80.C, J42.2, J42.8, R202.1, R203.1, R204.1, R205.1, R206.1, R207.1, R208.1, R209.1, R210.1, U21.8, U21.9, U21.14, U21.PAD
GND21: C64.2, C65.2, C66.2, D84.C, J44.2, J44.8, R212.1, R213.1, R214.1, R215.1, R216.1, R217.1, R218.1, R219.1, R220.1, U22.8, U22.9, U22.14, U22.PAD
GND22: C67.2, C68.2, C69.2, D88.C, J46.2, J46.8, R222.1, R223.1, R224.1, R225.1, R226.1, R227.1, R228.1, R229.1, R230.1, U23.8, U23.9, U23.14, U23.PAD
GND23: C70.2, C71.2, C72.2, D92.C, J48.2, J48.8, R232.1, R233.1, R234.1, R235.1, R236.1, R237.1, R238.1, R239.1, R240.1, U24.8, U24.9, U24.14, U24.PAD
GND24: C73.2, C74.2, C75.2, D96.C, J50.2, J50.8, R242.1, R243.1, R244.1, R245.1, R246.1, R247.1, R248.1, R249.1, R250.1, U25.8, U25.9, U25.14, U25.PAD
GND25: C76.2, C77.2, C78.2, D100.C, J52.2, J52.8, R252.1, R253.1, R254.1, R255.1, R256.1, R257.1, R258.1, R259.1, R260.1, U26.8, U26.9, U26.14, U26.PAD
GND26: C79.2, C80.2, C81.2, D104.C, J54.2, J54.8, R262.1, R263.1, R264.1, R265.1, R266.1, R267.1, R268.1, R269.1, R270.1, U27.8, U27.9, U27.14, U27.PAD
GND27: C82.2, C83.2, C84.2, D108.C, J56.2, J56.8, R272.1, R273.1, R274.1, R275.1, R276.1, R277.1, R278.1, R279.1, R280.1, U28.8, U28.9, U28.14, U28.PAD
GND28: C85.2, C86.2, C87.2, D112.C, J58.2, J58.8, R282.1, R283.1, R284.1, R285.1, R286.1, R287.1, R288.1, R289.1, R290.1, U29.8, U29.9, U29.14, U29.PAD
GND29: C88.2, C89.2, C90.2, D116.C, J60.2, J60.8, R292.1, R293.1, R294.1, R295.1, R296.1, R297.1, R298.1, R299.1, R300.1, U30.8, U30.9, U30.14, U30.PAD
unnamed: R3.2, V.1
unnamed: R1.2, V1.1
unnamed: D2.A, R1.1
unnamed: D1.A, R3.1
unnamed: D3.A, S.1
unnamed: C5.1, U2.13
unnamed: C6.1, U1.13
unnamed: D5.1, D7.A
unnamed: D.1, D4.A
unnamed: D3.C, R4.2
unnamed: D6.A, S1.1
unnamed: D4.C, R14.2
unnamed: D7.C, R18.2
unnamed: D6.C, R19.2
unnamed: R21.2, V2.1
unnamed: D8.A, R21.1
unnamed: C9.1, U3.13
unnamed: D9.1, D11.A
unnamed: D10.A, S2.1
unnamed: D11.C, R28.2
unnamed: D10.C, R29.2
unnamed: R31.2, V3.1
unnamed: D12.A, R31.1
unnamed: C12.1, U4.13
unnamed: D13.1, D15.A
unnamed: D14.A, S3.1
unnamed: D15.C, R38.2
unnamed: D14.C, R39.2
unnamed: R41.2, V4.1
unnamed: D16.A, R41.1
unnamed: C15.1, U5.13
unnamed: D17.1, D19.A
unnamed: D18.A, S4.1
unnamed: D19.C, R48.2
unnamed: D18.C, R49.2
unnamed: R51.2, V5.1
unnamed: D20.A, R51.1
unnamed: C18.1, U6.13
unnamed: D21.1, D23.A
unnamed: D22.A, S5.1
unnamed: D23.C, R58.2
unnamed: D22.C, R59.2
unnamed: R61.2, V6.1
unnamed: D24.A, R61.1
unnamed: C21.1, U7.13
unnamed: D25.1, D27.A
unnamed: D26.A, S6.1
unnamed: D27.C, R68.2
unnamed: D26.C, R69.2
unnamed: R71.2, V7.1
unnamed: D28.A, R71.1
unnamed: C24.1, U8.13
unnamed: D29.1, D31.A
unnamed: D30.A, S7.1
unnamed: D31.C, R78.2
unnamed: D30.C, R79.2
unnamed: R81.2, V8.1
unnamed: D32.A, R81.1
unnamed: C27.1, U9.13
unnamed: D33.1, D35.A
unnamed: D34.A, S8.1
unnamed: D35.C, R88.2
unnamed: D34.C, R89.2
unnamed: R91.2, V9.1
unnamed: D36.A, R91.1
unnamed: C30.1, U10.13
unnamed: D37.1, D39.A
unnamed: D38.A, S9.1
unnamed: D39.C, R98.2
unnamed: D38.C, R99.2
unnamed: R101.2, V10.1
unnamed: D40.A, R101.1
unnamed: C33.1, U11.13
unnamed: D41.1, D43.A
unnamed: D42.A, S10.1
unnamed: D43.C, R108.2
unnamed: D42.C, R109.2
unnamed: R111.2, V11.1
unnamed: D44.A, R111.1
unnamed: C36.1, U12.13
unnamed: D45.1, D47.A
unnamed: D46.A, S11.1
unnamed: D47.C, R118.2
unnamed: D46.C, R119.2
unnamed: R121.2, V12.1
unnamed: D48.A, R121.1
unnamed: C39.1, U13.13
unnamed: D49.1, D51.A
unnamed: D50.A, S12.1
unnamed: D51.C, R128.2
unnamed: D50.C, R129.2
unnamed: R131.2, V13.1
unnamed: D52.A, R131.1
unnamed: C42.1, U14.13
unnamed: D53.1, D55.A
unnamed: D54.A, S13.1
unnamed: D55.C, R138.2
unnamed: D54.C, R139.2
unnamed: R141.2, V14.1
unnamed: D56.A, R141.1
unnamed: C45.1, U15.13
unnamed: D57.1, D59.A
unnamed: D58.A, S14.1
unnamed: D59.C, R148.2
unnamed: D58.C, R149.2
unnamed: R151.2, V15.1
unnamed: D60.A, R151.1
unnamed: C48.1, U16.13
unnamed: D61.1, D63.A
unnamed: D62.A, S15.1
unnamed: D63.C, R158.2
unnamed: D62.C, R159.2
unnamed: R161.2, V16.1
unnamed: D64.A, R161.1
unnamed: C51.1, U17.13
unnamed: D65.1, D67.A
unnamed: D66.A, S16.1
unnamed: D67.C, R168.2
unnamed: D66.C, R169.2
unnamed: R171.2, V17.1
unnamed: D68.A, R171.1
unnamed: C54.1, U18.13
unnamed: D69.1, D71.A
unnamed: D70.A, S17.1
unnamed: D71.C, R178.2
unnamed: D70.C, R179.2
unnamed: R181.2, V18.1
unnamed: D72.A, R181.1
unnamed: C57.1, U19.13
unnamed: D73.1, D75.A
unnamed: D74.A, S18.1
unnamed: D75.C, R188.2
unnamed: D74.C, R189.2
unnamed: R191.2, V19.1
unnamed: D76.A, R191.1
unnamed: C60.1, U20.13
unnamed: D77.1, D79.A
unnamed: D78.A, S19.1
unnamed: D79.C, R198.2
unnamed: D78.C, R199.2
unnamed: R201.2, V20.1
unnamed: D80.A, R201.1
unnamed: C63.1, U21.13
unnamed: D81.1, D83.A
unnamed: D82.A, S20.1
unnamed: D83.C, R208.2
unnamed: D82.C, R209.2
unnamed: R211.2, V21.1
unnamed: D84.A, R211.1
unnamed: C66.1, U22.13
unnamed: D85.1, D87.A
unnamed: D86.A, S21.1
unnamed: D87.C, R218.2
unnamed: D86.C, R219.2
unnamed: R221.2, V22.1
unnamed: D88.A, R221.1
unnamed: C69.1, U23.13
unnamed: D89.1, D91.A
unnamed: D90.A, S22.1
unnamed: D91.C, R228.2
unnamed: D90.C, R229.2
unnamed: R231.2, V23.1
unnamed: D92.A, R231.1
unnamed: C72.1, U24.13
unnamed: D93.1, D95.A
unnamed: D94.A, S23.1
unnamed: D95.C, R238.2
unnamed: D94.C, R239.2
unnamed: R241.2, V24.1
unnamed: D96.A, R241.1
unnamed: C75.1, U25.13
unnamed: D97.1, D99.A
unnamed: D98.A, S24.1
unnamed: D99.C, R248.2
unnamed: D98.C, R249.2
unnamed: R251.2, V25.1
unnamed: D100.A, R251.1
unnamed: C78.1, U26.13
unnamed: D101.1, D103.A
unnamed: D102.A, S25.1
unnamed: D103.C, R258.2
unnamed: D102.C, R259.2
unnamed: R261.2, V26.1
unnamed: D104.A, R261.1
unnamed: C81.1, U27.13
unnamed: D105.1, D107.A
unnamed: D106.A, S26.1
unnamed: D107.C, R268.2
unnamed: D106.C, R269.2
unnamed: R271.2, V27.1
unnamed: D108.A, R271.1
unnamed: C84.1, U28.13
unnamed: D109.1, D111.A
unnamed: D110.A, S27.1
unnamed: D111.C, R278.2
unnamed: D110.C, R279.2
unnamed: R281.2, V28.1
unnamed: D112.A, R281.1
unnamed: C87.1, U29.13
unnamed: D113.1, D115.A
unnamed: D114.A, S28.1
unnamed: D115.C, R288.2
unnamed: D114.C, R289.2
unnamed: R291.2, V29.1
unnamed: D116.A, R291.1
unnamed: C90.1, U30.13
unnamed: D117.1, D119.A
unnamed: D118.A, S29.1
unnamed: D119.C, R298.2
unnamed: D118.C, R299.2
SENSE: J2.6, R15.2, U2.16, U2.20
SENSE1: J4.6, R20.2, U1.16, U1.20
SENSE2: J6.6, R30.2, U3.16, U3.20
SENSE3: J8.6, R40.2, U4.16, U4.20
SENSE4: J10.6, R50.2, U5.16, U5.20
SENSE5: J12.6, R60.2, U6.16, U6.20
SENSE6: J14.6, R70.2, U7.16, U7.20
SENSE7: J16.6, R80.2, U8.16, U8.20
SENSE8: J18.6, R90.2, U9.16, U9.20
SENSE9: J20.6, R100.2, U10.16, U10.20
SENSE10: J22.6, R110.2, U11.16, U11.20
SENSE11: J24.6, R120.2, U12.16, U12.20
SENSE12: J26.6, R130.2, U13.16, U13.20
SENSE13: J28.6, R140.2, U14.16, U14.20
SENSE14: J30.6, R150.2, U15.16, U15.20
SENSE15: J32.6, R160.2, U16.16, U16.20
SENSE16: J34.6, R170.2, U17.16, U17.20
SENSE17: J36.6, R180.2, U18.16, U18.20
SENSE18: J38.6, R190.2, U19.16, U19.20
SENSE19: J40.6, R200.2, U20.16, U20.20
SENSE20: J42.6, R210.2, U21.16, U21.20
SENSE21: J44.6, R220.2, U22.16, U22.20
SENSE22: J46.6, R230.2, U23.16, U23.20
SENSE23: J48.6, R240.2, U24.16, U24.20
SENSE24: J50.6, R250.2, U25.16, U25.20
SENSE25: J52.6, R260.2, U26.16, U26.20
SENSE26: J54.6, R270.2, U27.16, U27.20
SENSE27: J56.6, R280.2, U28.16, U28.20
SENSE28: J58.6, R290.2, U29.16, U29.20
SENSE29: J60.6, R300.2, U30.16, U30.20
U: J2.3, U2.15
U1: J4.3, U1.15
U2: J6.3, U3.15
U3: J8.3, U4.15
U4: J10.3, U5.15
U5: J12.3, U6.15
U6: J14.3, U7.15
U7: J16.3, U8.15
U8: J18.3, U9.15
U9: J20.3, U10.15
U10: J22.3, U11.15
U11: J24.3, U12.15
U12: J26.3, U13.15
U13: J28.3, U14.15
U14: J30.3, U15.15
U15: J32.3, U16.15
U16: J34.3, U17.15
U17: J36.3, U18.15
U18: J38.3, U19.15
U19: J40.3, U20.15
U20: J42.3, U21.15
U21: J44.3, U22.15
U22: J46.3, U23.15
U23: J48.3, U24.15
U24: J50.3, U25.15
U25: J52.3, U26.15
U26: J54.3, U27.15
U27: J56.3, U28.15
U28: J58.3, U29.15
U29: J60.3, U30.15
UH: J1.6, R10.2, U2.3
UH1: J3.6, R17.2, U1.3
UH2: J5.6, R27.2, U3.3
UH3: J7.6, R37.2, U4.3
UH4: J9.6, R47.2, U5.3
UH5: J11.6, R57.2, U6.3
UH6: J13.6, R67.2, U7.3
UH7: J15.6, R77.2, U8.3
UH8: J17.6, R87.2, U9.3
UH9: J19.6, R97.2, U10.3
UH10: J21.6, R107.2, U11.3
UH11: J23.6, R117.2, U12.3
UH12: J25.6, R127.2, U13.3
UH13: J27.6, R137.2, U14.3
UH14: J29.6, R147.2, U15.3
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

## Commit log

2022-09-21 Add PROD IDs
    [SparkFun_TMC6300_Breakout.brd, SparkFun_TMC6300_Breakout.sch]
2022-09-23 Fix pinout to emulate other reprap style drivers
    [SparkFun_TMC6300_Breakout.brd, SparkFun_TMC6300_Breakout.sch]
2022-09-23 Fix DIAG label direction
    [SparkFun_TMC6300_Breakout.brd]
2022-10-20 Add production files
    [SparkFun_TMC6300_Breakout-BottomJig.GBL, SparkFun_TMC6300_Breakout-BottomJig.GBO, SparkFun_TMC6300_Breakout-BottomJig.GBP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]
2022-12-12 Add readme. Remove old files.
    [SparkFun_TMC6300_Breakout-BottomJig.brd, SparkFun_TMC6300_Breakout.brd]

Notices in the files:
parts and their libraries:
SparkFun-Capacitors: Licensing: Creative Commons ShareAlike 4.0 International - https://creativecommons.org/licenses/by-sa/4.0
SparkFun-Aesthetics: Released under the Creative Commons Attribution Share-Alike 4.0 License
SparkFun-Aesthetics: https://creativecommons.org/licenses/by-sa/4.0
